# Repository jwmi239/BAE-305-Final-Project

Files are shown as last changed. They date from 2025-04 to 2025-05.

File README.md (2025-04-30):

# BAE-305-Final-Project
This repository contains all of the files associated with the BAE 305 final project.
## Project Summary

This report outlines the design, creation, and testing of a remote-control (RC) car intended for both the use of children and RC enthusiasts. In the original design concept, the user was intended to use radio connections to wirelessly control a four-wheel-drive, four-wheel-steer RC car programmed and powered by an Arduino Uno microcontroller. Additional features originally included a speedometer, a visual display, and car noises corresponding with the acceleration of the car. In the final product, the car was two-wheel-drive and two-wheel-steer and included features such as a handheld Bluetooth controller (as opposed to radio), an ultrasonic sensor serving as a safety feature, and a horn that plays the UK fight song. Through various testing phases, such as testing motor control via Bluetooth and iterating steering control to improve alignment, the RC car was completed and fully functional. 

## Design Description

### Bluetooth Wireless Connection

#### Materials

- HC-05 Bluetooth Module  
- Breadboard  
- Jumper wires  
- Raspberry Pi 3  
- Arduino Uno  
- 8BitDo Zero 2 Controller  

#### Assembly Procedures

First, the communication between the Raspberry Pi 3 and Arduino Uno was created. Once the HC-05 Bluetooth module was acquired, it was plugged into a breadboard and wired to the Arduino via jumper wires. It was connected to the 5V power rail and ground, the RX pin was connected to the software TX port, and the TX pin was connected to the software RX port. On the Raspberry Pi, no additional hardware was needed, as it has native Bluetooth capabilities. Serial communication and Bluetooth pairing were enabled by modifying the /boot/config.txt and disabling the serial console via raspi-config and using the bluetoothctl menu. The HC-05 was put in pairing mode by pressing and holding its button while powering it, which caused the onboard LED to blink rapidly. The Raspberry Pi then scanned for devices, paired with the HC-05, and trusted the connection. Once paired, the HC-05 was assigned a virtual serial port (e.g., /dev/rfcomm0), which is called in the main Python script. 

Once this connection was made, the 8BitDo Zero 2 gamepad was integrated via a wired USB connection to the Raspberry Pi. The controller was initialized in D-Input mode by holding the Start + Y buttons before connection, allowing it to register as a standard USB gamepad. Once connected, the Raspberry Pi automatically recognized the controller as /dev/input/js0. Functionality was verified using the jstest utility. Python was used to display button inputs to map button and directional inputs to specific vehicle actions, such as motor direction and auxiliary functions (playing the UK fight song).  



Figure 1: HC-05 Wiring Diagram

### Ultrasonic Sensor 

#### Materials
-	HC-sr04 ultrasonic distance sensor
-	4 male-female jumper cables
#### Assembly Procedures
Connect all four jumper cables to the HC-sr04, ensuring to note which wires connect to certain pins (Ideally using color coding to distinguish functions, such as red for power and black for ground). Connect the VCC pin of the Ultrasonic distance sensor to the 5V source of the Arduino. Connect the GND pin of the Ultrasonic distance sensor to any of the ground pins on the Arduino. Connect the Trig pin on the ultrasonic distance sensor to pin 6 on the Arduino, and the Echo pin to pin 7 on the Arduino. Ensure that each of the pins are connected to the correct pin on the Arduino before powering on.
### Steering

#### Materials
  -	¼” – 20 tpi Hardware
  -	3D printed Steering Components
    -	Steering Knuckles
    -	Drag Links
    -	Front Carriage
  -	SG90 Servo and Included Lever (Pitman arm)
  -	1/8” Cotter Pins

#### Assembly Procedures
The steering system is simple to assemble, creating an intuitive assembly and maintenance process. 

Step 1: Bolt the front carriage under the base of the car using three ¼” bolts



Figure 2: Steering System Assembly Step 1

Step 2: Install steering knuckle on each side of the front carriage using two ¼” bolts



Figure 3: Steering System Assembly Step 2

Step 3: Bolt Servo mount to base of car using two ¼” bolts and install the servo



Figure 4: Steering System Assembly Step 3

Step 4: Connect the servo to each steering knuckle with respected drag links, cotter pin each connection



Figure 5: Steering System Assembly Step 4

Step 5: Bolt wheels to the outside face of each steering knuckle using a ¼” bolt



Figure 6: Steering System Assembly Step 5

Step 6: The servo is then wired using 5V for power, one power signal from a PWM pin, and a ground. The Arduino is coded to send an output for left and right turns at 45° based on the input from the controller. 



Figure 7: Steering Servo Wiring Schematic

### Body

#### Materials
-	3D printed components
    -	Cab 
    -	Front Clip
    -	Bed 
    -	Bed Cover
-	SparkFun inventor’s kit
    -	Motor driver
    -	Motor x2
-	9V battery

#### Assembly Procedures
The body was designed to be easily assembled and removed. There is a ridge formed along the bottom of each body panel which simply slides over the aluminum base plate. When each body panel has been attached to the base, route the wires between the bottom of the bed and the base plate and connect them according to the schematic below. Finally, turn the battery packs on and place the bed cover in position to shield the electrical components.



Figure 8: Wiring for Motors and Motor Driver

### Speakers

#### Materials

- Arduino 
- DFPlayer Mini 
- 1W 8 Ohm speaker 
- 680 Ohm resistor 
- 1K Ohm resistor 
- 9V battery 
- 8705 Voltage Regulator 

#### Assembly Procedures

The Speaker assembly consisted of multiple interconnected pieces. The wiring can be found in Figure 9. First, the Arduino was connected to the RX and TX pins of the DFPlayer mini. The RX of the player was connected through a parallel circuit that had two paths starting from the Arduino digital pin. The first path ran through a 680 resistor then split to the player. The second path after running through the 680 resistor, ran through a 1K resistor and to ground. This allowed the Arduino to control when the player functioned. The player controlled the sound, sourcing it to a 1W speaker to amplify the sound. The speaker connected to the SPK1 and SPK2 pins in the player. To power the speaker, a 9V battery was wired as the power source. The battery ran through a voltage regulator to set 5V and 1.5A to the DFPlayer. The voltage regulator output pin connected to the Vin of the player, supplying the necessary power to run the speaker. 

The Arduino IDE code used a downloadable DFPlayer library. After a few set up functions, the DFPlayer Mini could play a specific file from the command “MP3player.play(#)” where # corresponds to the desired sound file number. Sound functions within the system at three separate points. The player functions from the second Arduino. First, an engine sound plays resulting from changes in acceleration. The DFPlayer command was integrated into an if statement for when the accelerometer reads a value above a threshold. The other two sounds, the UK fight song and the reverse sound, function in the same way—however the logic set to run them are found on the first Arduino. The Arduino 1 code sends a signal to Arduino 2 when a specific button is pressed for the fight song and the car is reversing for the reversing sound. Each sound plays through the audio file. The full code can be found in Results. 

ChatGPT Image Apr 24, 2025, 07_51_10 PM

Figure 9: Circuit Diagram for the sound components of the RC car. This wiring diagram was generated by ChatGPT 4o Ai

### Lights

#### Materials

- LED x2 
- 1K Ohm resistor x2 

#### Assembly Procedures

Two LEDs were added to the car in the same way. The circuit for these LED’s are simple and direct, with few components. Fed power from the Arduino, the circuit path flows from a digital pin to the 1K resistor in the breadboard, to the LED, to ground. The LED’s did not share a digital pin, as to allow them to be controlled separately. For the circuit diagram, see Figure 10.

LED circuit diagram image

Figure 10: Circuit Diagram for the LED circuit. This is repeated for the second LED circuit

## Design Discussion

### Bluetooth

Bluetooth was chosen as the means for communication rather than traditional radio. While traditional radio does not require pairing or draw the amount of power that Bluetooth does, Bluetooth was chosen for its ease of integration with both of the microcontrollers being used in the project. The Pi is natively compatible with Bluetooth devices, and the Arduino merely needed an inexpensive Bluetooth module (HC-05). Apart from the occasional disconnection due to the power demands of the module, this made connection seamless after the initial connection to the Pi was made.  

Future designs may employ Bluetooth for additional features to the car. Supplemental power sources may be needed to prevent the disconnection of the module from the Pi. 

### Distance Sensing

### Steering
To create a more realistically functioning car, we decided to model the steering after a two-wheel bell crank. The bell crank method uses a two-link system connected to each wheel that allows both wheels to turn from a single servo, similar to actual automobiles. This is done through a series of steering components, which includes a pitman arm, steering knuckles, and drag links. The goal with this system was to create what is known as Ackermann geometry. A steering system is considered to be Ackermann steering if the inside wheel is at a sharper angle than the outside wheel while turning. This is the case with the bell crank system, as seen below.



Figure 11: Ackermann Steering Angle Phenomenon

With the pitman arm at a center-point, equal length drag links, and mirrored geometry for the steering knuckles, this creates a sharper angle for the side that the servo is turning away from. If not for this phenomenon, the inside wheel would be fighting the ground during turns due to travelling on a smaller turning radii than the outside wheel, as shown below. Ackermann steering allows for less wear on tires, steering components, and axle gearing if applicable. 



Figure 12: Inside wheel vs. Outside wheel Turning Radius 
### Sound

The car contains a sound component that functions as a final output for multiple logic systems. The sound for the car functions through a DFPlayer Mini. The DFPlayer is an MP3 module for the Arduino. The DFPlayer Mini was chosen as the sound playing device because of its easy integration with the Arduino system. Arduino IDE has a downloadable library for the DFplayer that allows audio to be integrated into the code with a few simple commands. For this application, the DFPlayer Mini connects to a 1W speaker that projects the sound. Housing a micro-SD card, the player runs MP3 audio files when directed by the Arduino microcontroller.  A voltage regulator and 9V battery were used to ensure the system received adequate power. The 9V supplied the voltage, and the regulator ensured adequate current flowed through the DFPlayer and to the speaker.  

### Lights

Lights were an added design feature of the car. These lights were to signal as the car turned. LED’s were chosen because they are often used in Arduino projects, and the bright colors add an additional sensory element for users. Individual LED’s were chosen over a strip of lights due to the high demand for current needed to sustain brightness in a longer string of LED’s. The entire car already had 9V batteries and 5V power packs, so it was determined unnecessary to add additional power sources for just the lights. Additionally, the singular LED’s mimicked the turn signals of a car, fitting well with the theme for the project. 

## Testing Procedures

The testing of the car took place in several phases as each feature was completed, as well as a final “sprint” to integrate all features.  

The first feature to be completed was the establishment of the wireless connection. A series of tests were completed for each leg of communication previously mentioned. First, the communication between the Raspberry Pi 3 and Arduino Uno was tested. Once the HC-05 Bluetooth module was running on the Arduino, serial communications were opened on both the Arduino and Pi. The HC-05, acting as the slave, was sent serial messages via the assigned serial port from the Pi to confirm its connection. Once the connection between the Pi and Arduino was secured, attention was turned to connecting the 8BitDo controller to the Pi. The controller was wired to the Pi via USB—similar to how a keyboard would work with the Pi. To determine what messages each button of the controller was sending upon being pressed, a short python script was created and used to read the button press events. These outputs were recorded and used in the development of the primary code. 

Another feature that needed to be completed and tested was sound. Initially, based on the DFPlayer specifications a 3W speaker was chosen. This speaker was the top of the power output range for the player. When in a system that ran solely the DFPlayer and the speaker, the sound worked without issues. When integrating with the system however, the speaker size proved to be an issue. Given the power demand of the 3W speaker, the addition of the sound system was creating a power need that exceeded the output capabilities of the Arduino. Consequently, the sound quality decreased, and other components of the car would not run when the speaker was playing. The necessary solution was switching to a different speaker that could use a smaller amount of power. Therefore, a 1W speaker was selected to replace the 3W speaker. This speaker was wired in the same way as the original speaker. This set up worked the first day it was implemented, however the following day had additional issues: giving loud low pitch feedback and not playing the desired mp3 files. A 9V battery was added to be the power source for the player and speaker. Wired through the Arduino however, this did not fix the issue as the Arduino limited the current flow of the circuit. To resolve this issue, a voltage regulator was incorporated. The voltage regulator connected to the 9V rather than the Arduino, supplying a 5V and 1.5 A to the DFPlayer and speaker. This resolved the sound issues. 

Lights were another feature that needed to be tested and integrated. Initially, it was planned to use an LED strip to maximize the appeal of the LED. In the inital testing of the LEDs it was determined that 5V from the Arduino was not sufficient to run the strip. This LED strip would require an additional power source to supply enough current to maintain light for many LEDs. Once additional power sources were acquired for the motors, the LEDs were revisited to see if they could be powered. During this testing, a 9V battery was wired through the 5V pin of the Arduino rather than the necessary Vin pin. This issue caused the computer connected to the Arduino to receive 9V of back voltage and stop working. Individual LEDs were chosen to be used over the strip due to the lack of need for additional power. These LEDs wired directly to the Arduino and were controlled from HIGH and LOW commands through a digital pin. 

The steering system also proposed a few challenges. The code was simple, just a few lines taken from online sources and tailored to the needs of this project. The CAD modeling resulted in relatively smooth implementation of the moving parts. However, the first iteration of the steering knuckles did not have clearance for the “lug nuts” and required more drop to allow for them. Connection methods for the drag links were also a point of testing. The holes were too small to reasonably use bolts and screws would’ve inhibited the rotation during turning. 

## Results



Figure 13: Complete car assembly

## Discussion

Throughout the project, there were multiple challenges and complications that needed to be overcome to complete the deliverables. These challenges molded the final project into what is presented in this report. The WildCar completed each deliverable it set out to do: two-wheel drive, two-wheel steering, wireless Bluetooth control, Lights synced to turning, revving sound from acceleration, beeping upon reversing, playing a song from a controlled input, and stop when too close to an object-- all integrated into a covered complete car design. 

Bluetooth control of the car proved to be both one of the most prominent features and drawbacks of the car. Proving difficult to set up and maintain manually, Bluetooth through a Raspberry Pi was an effective means of remote communication when connected. The system communicated with little delay and the signal transmitted without error. Bluetooth as incorporated in this system, however, had many drawbacks that would limit how well the project could be extrapolated to other projects. First, the connection needed to be manually established. The connection would often get lost, and the connection process repeated. Additionally, using the Pi as a relay from the controller and communicator to the Arduino proved to be an added layer of complexity. Navigating the Pi system was not user friendly and minimally added to the effectiveness of the project. While it did increase the range of connection when compared to the controller and Arduino alone, it was still limited by the inherent limitations of Bluetooth (about 30ft). Higher quality controllers or radio controllers are available for purchase that have greater range, and can cut out the Pi as an intermediate, effectively communicating directly with the Arduino. 

Another limitation with the WildCar design is in regard to power. The Ardunos are only capable of 5V power output with a power pack. Many parts of the design required greater power to run sufficiently when integrated. The final design required two 5V power packs and two 9V batteries. The design was limited by these sources because the batteries would quickly drain and require replacement. The power sources, whilst rechargeable, faced similar issues. The system did supply power effectively, and each component functioned properly with the power supplied. Multiple sources also allowed for each component to receive the specific power needed independently. Performance would decrease as the power drained. A higher quality single power supply would allow for a more integrated design, would last longer, and clean up the wiring. As seen in the use of a voltage regulator to meet the specific needs of the speaker, power output could be modified as needed to meet individual needs of components. A better power supply would also allow the car to run longer at full performance.  

The code for the steering system worked as expected with the lines given online. Integration was easy, as the controller was already connected via Bluetooth to send input to the servo. Another easy fix came through the implementation of cotter pins for the linkage connections; the pins are small enough and allow for rotation during turning. The last step was to add clearance for the lug nuts, which was done through a second iteration of 3D printed steering knuckles. This allowed for tightening of the entire steering system, and brought the car closer to having true Ackermann steering geometry.

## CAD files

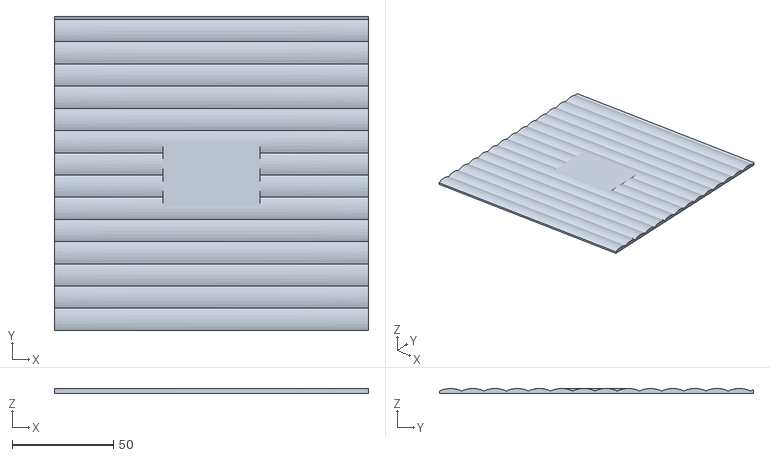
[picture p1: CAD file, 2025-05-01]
Truck cover.stl
155.0 x 155.0 x 2.50

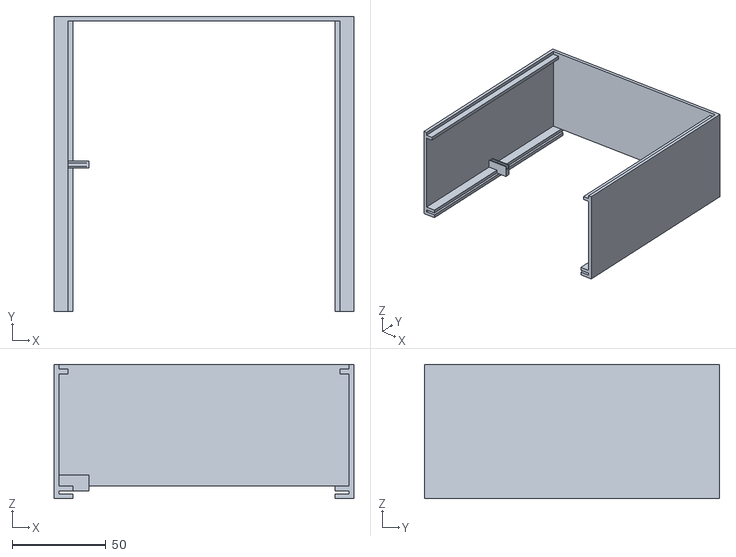
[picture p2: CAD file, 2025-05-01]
TruckBed.stl
160.0 x 157.5 x 71.5

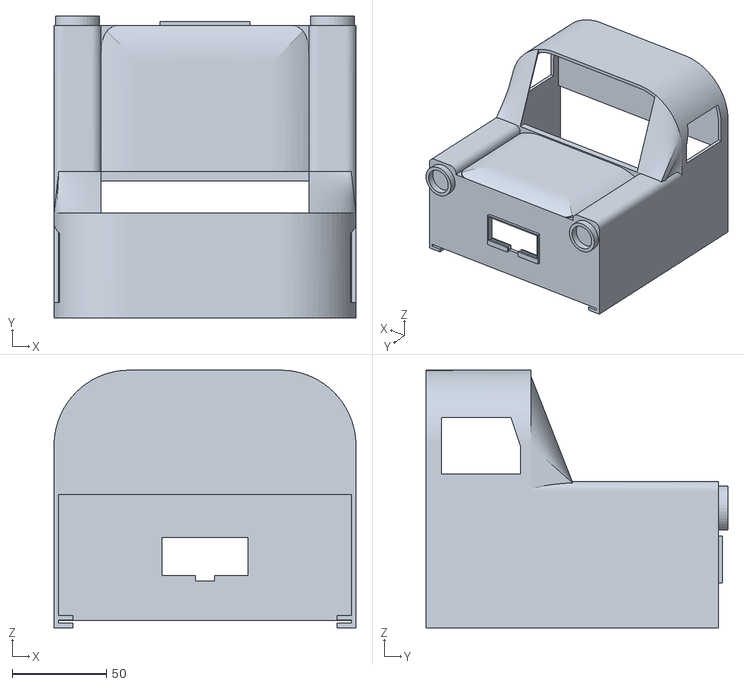
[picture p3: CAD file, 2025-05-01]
CarFront.stl
160.0 x 160.0 x 136.6

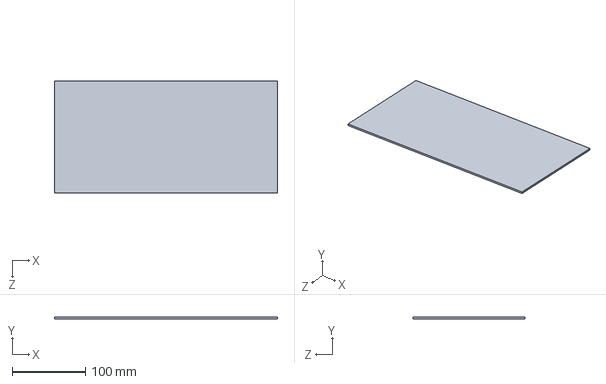
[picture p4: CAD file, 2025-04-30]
BAE 305 Car Frame.SLDPRT
304.8 x 2.54 x 152.4 mm

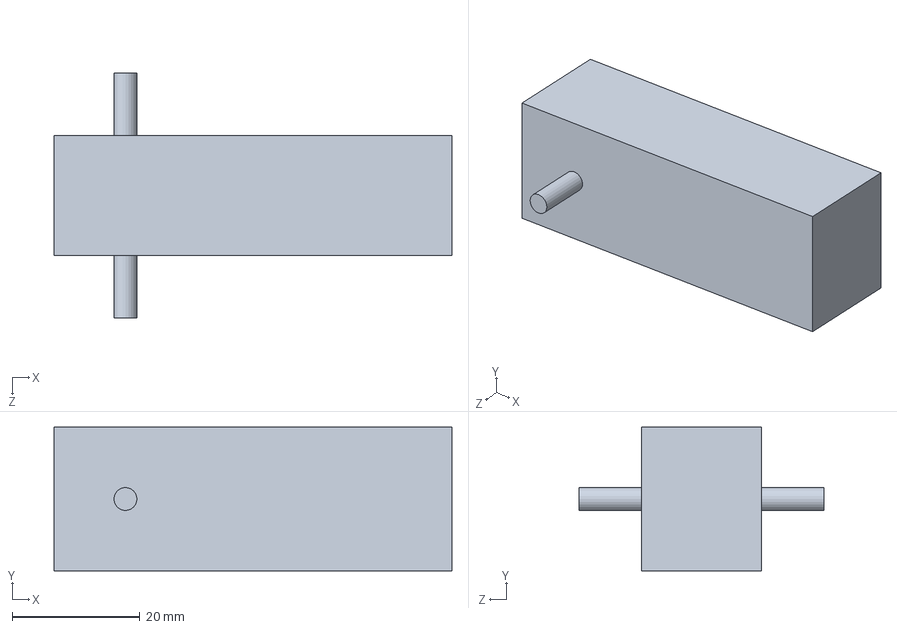
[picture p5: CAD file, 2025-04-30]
BAE 305 Motor.SLDPRT
62.4 x 22.5 x 38.4 mm

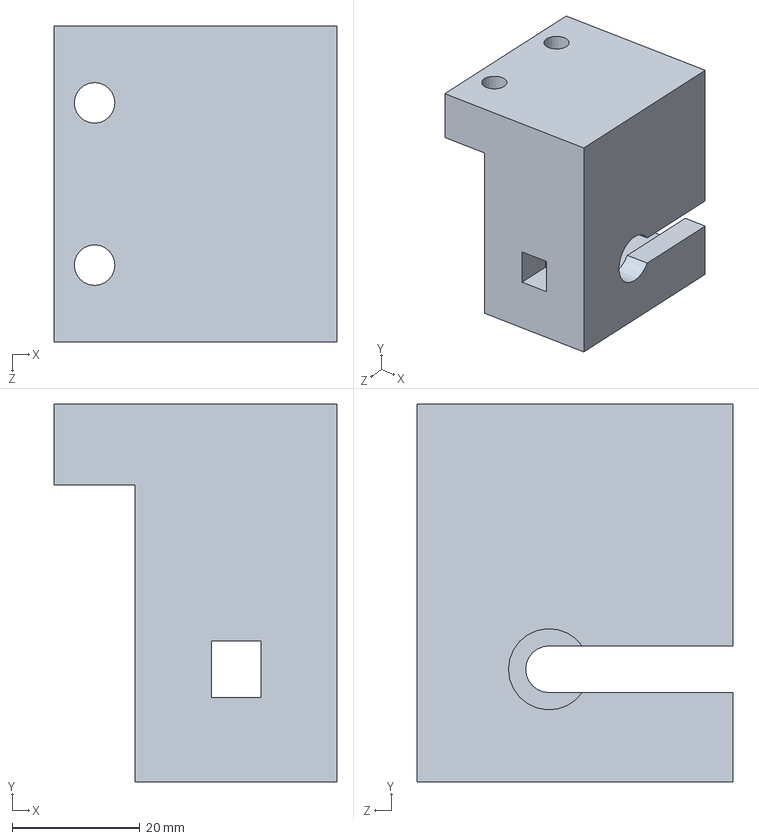
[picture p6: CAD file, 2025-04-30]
BAE 305 Car Passenger Motor mount.SLDPRT
44.3 x 59.2 x 49.5 mm

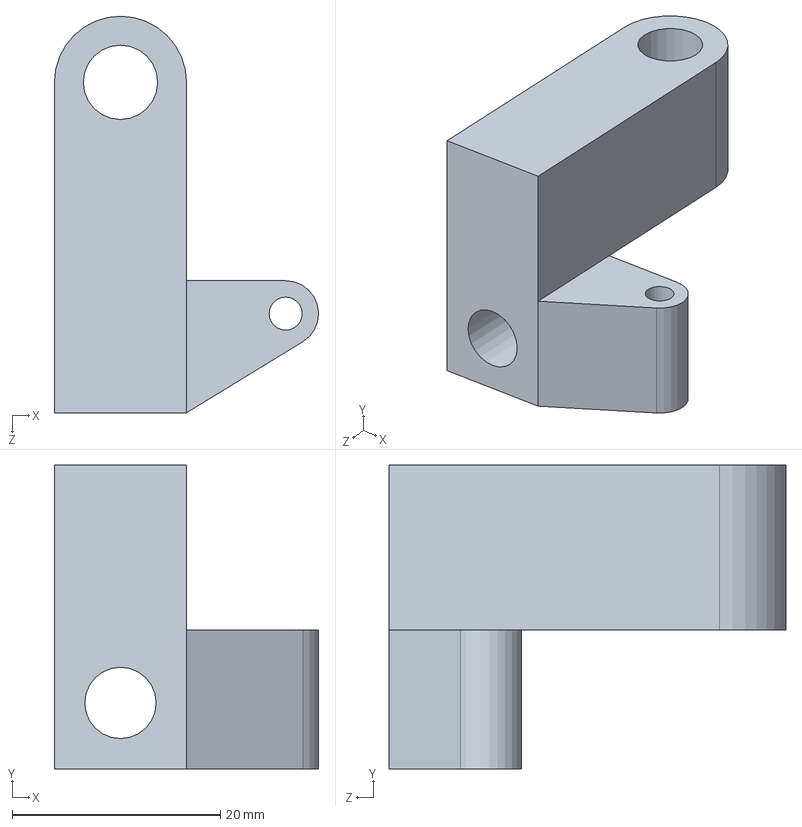
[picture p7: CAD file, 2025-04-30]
BAE 305 Steering Knuckle.SLDPRT
25.4 x 29.2 x 38.1 mm

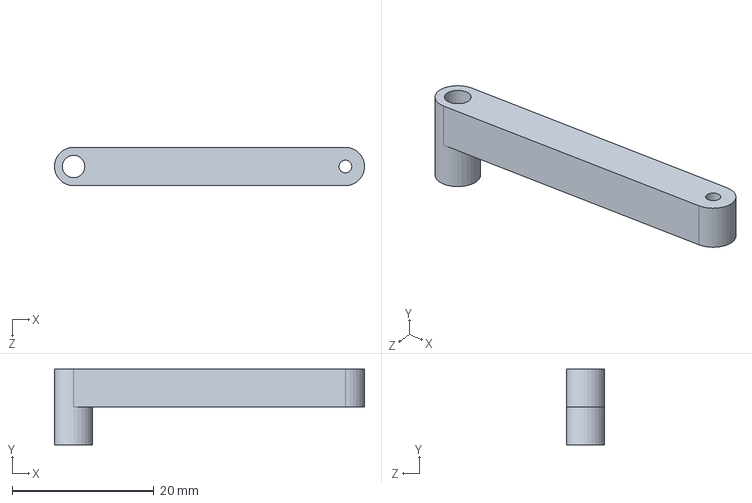
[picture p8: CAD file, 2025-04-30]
BAE 305 Tie Rod Passenger.SLDPRT
43.7 x 10.7 x 5.40 mm

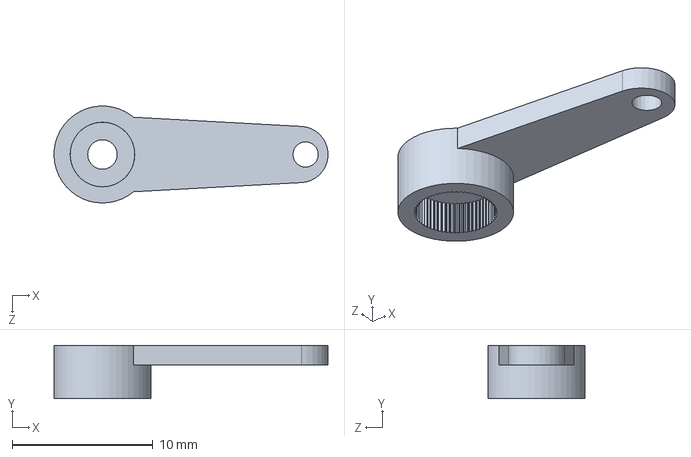
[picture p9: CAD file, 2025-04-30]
SG90 Arm.SLDPRT
19.5 x 3.80 x 6.90 mm

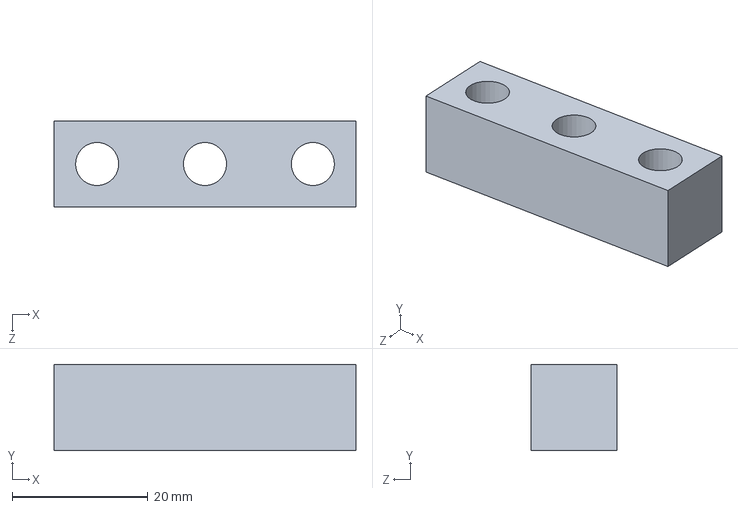
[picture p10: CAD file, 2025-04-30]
BAE 305 Front end bottom.SLDPRT
44.5 x 12.7 x 12.7 mm

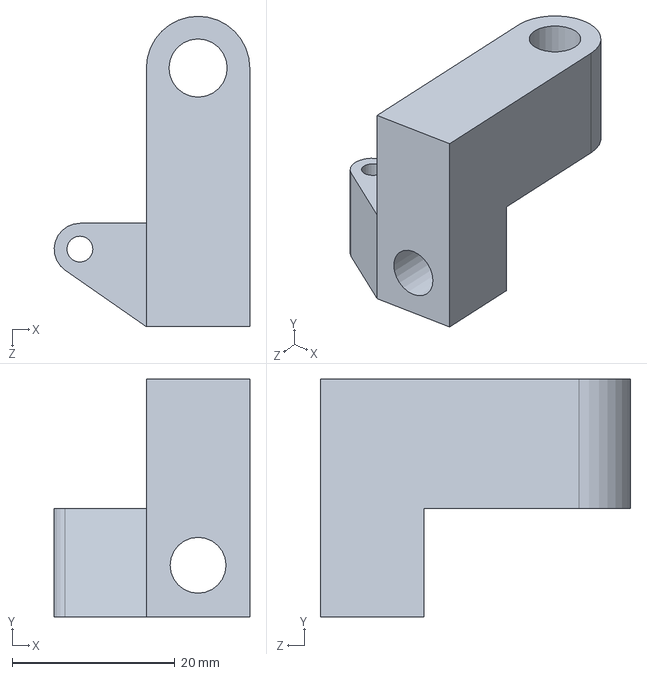
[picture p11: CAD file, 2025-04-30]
BAE 305 Opposite Steering Knuckle.SLDPRT
24.0 x 29.2 x 38.1 mm

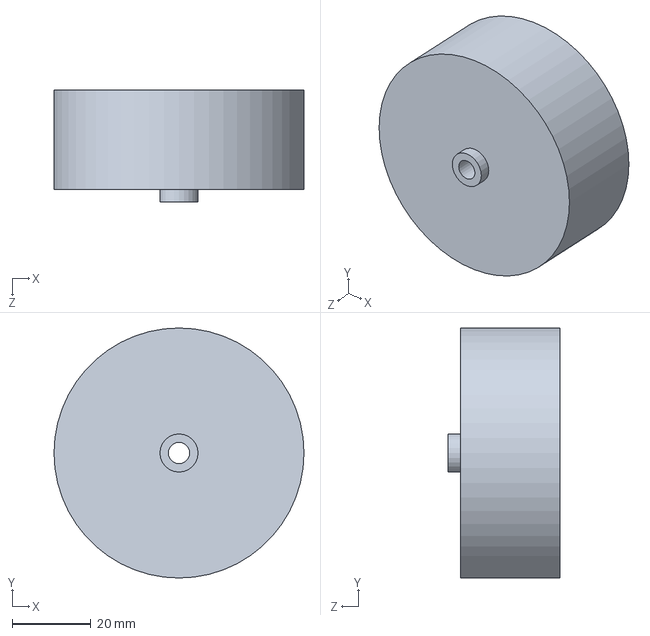
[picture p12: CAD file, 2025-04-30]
BAE 305 Wheels.SLDPRT
63.5 x 63.5 x 28.6 mm

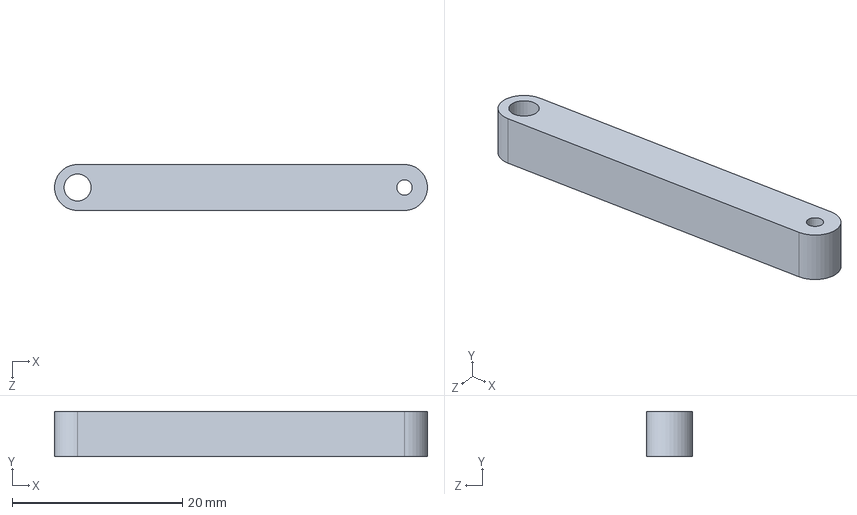
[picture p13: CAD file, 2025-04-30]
BAE 305 Tie Rods.SLDPRT
43.8 x 5.33 x 5.40 mm

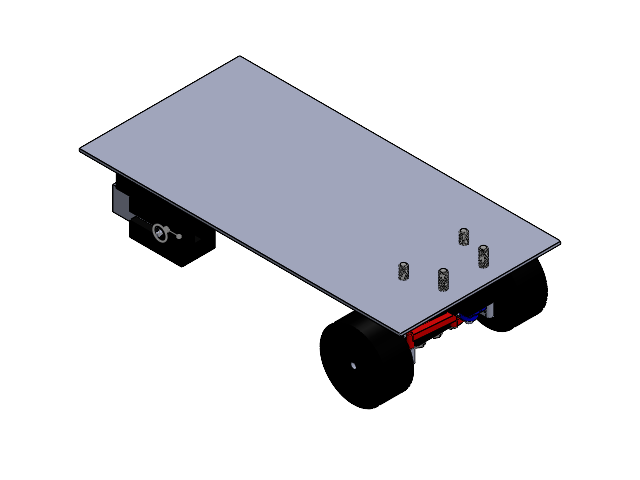
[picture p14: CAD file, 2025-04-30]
BAE 305 RC CAR.SLDASM
BAE 305 Car Frame
BAE 305 Motor
BAE 305 Wheels x 2
BAE 305 Steering Knuckle
BAE 305 Opposite Steering Knuckle
BAE 305 Car Front end
SG90 - MotorOutput
SG90 Arm
BAE 305 Tie Rods
BAE 305 Tie Rod Passenger
BAE 305 Servo mount
BAE 305 Front end bottom
92620A542_Zinc Yellow-Chromate Plated Hex Head Screw x 7
BAE 305 Car Passenger Motor mount
BAE 305 Car Driver Motor mount

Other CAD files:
BAE 305 Car Driver Motor mount.SLDPRT
BAE 305 Servo mount.SLDPRT
BAE 305 Car Front end.SLDPRT
SG90 - BasePart.sldprt
SG90 - MotorOutput.sldprt

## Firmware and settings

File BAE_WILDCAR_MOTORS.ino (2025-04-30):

#include <SoftwareSerial.h>                 //Imporing of necesarry Libraries
#include <Servo.h>

SoftwareSerial BTSerial(3,2);               // Bluetooth (RX,TX) as arduino sees it

const int trig = 4;                         // Pins for Ultrasonic distance sensor
const int echo = 5;                         //

const int LeftLED = 7;                      //Pins for turning signal LEDs
const int RightLED = 6;

const int AIN1 = 8;                         //Pins for motor Driver
const int AIN2 = 9;
const int PWMA = 10;
const int Servopin = 11;                    //Pin to control Servo motor

const int arduinoConnection1 = 12;          //Pins to connect to second arduino
const int arduinoConnection2 = 13;

Servo myServo;                              //Instantiates a servo object

int motorSpeed = 250;                       //initialization of global variables to be used by program
int centerPos = 90;
int leftPos = centerPos - 45;  
int rightPos = centerPos + 45; 
float duration, distance;
char command;

void setup() {
  pinMode(AIN1, OUTPUT);                    //Set pins associated with motor driver to be outputs
  pinMode(AIN2, OUTPUT);
  pinMode(PWMA, OUTPUT);
  pinMode(trig, OUTPUT);                    //Set pins for the Ultrasonic sensor to be input/output respectively for trigger and echo
  pinMode(echo, INPUT);
  pinMode(LeftLED,OUTPUT);                  //Set pins associated with LED indicators to be outputs
  pinMode(RightLED,OUTPUT);
  pinMode(arduinoConnection1,OUTPUT);       //set connection Pins to be output pins
  pinMode(arduinoConnection2,OUTPUT);

  BTSerial.begin(9600);                     //Begin serial communication with the HC-05
  myServo.attach(Servopin);                 //Tell the servo which pin it is attached to so that its internal methods function correctly 
  myServo.write(centerPos);                 //Write the location of the servo motor to be the center position that we want
  }

void loop() {
  
  digitalWrite(trig, LOW);                  //Trigger the Ultrasonic distance sensor to emit a recoverable signal
  delayMicroseconds(2);
  digitalWrite(trig, HIGH);
  delayMicroseconds(10);
  digitalWrite(trig, LOW);

  duration = pulseIn(echo, HIGH);           //Collect information about the ultrasonic signal and calculate the distance from the car to an obstacle
  distance = (duration*0.0343)/2;
  delay(100);
  
  if (distance <= 10 ){                    //Check if the car is too close to something
    if (BTSerial.available()) {            //Allow the car to check the bluetooth because the user will want to reverse still if they got too close to something

      command = (char)BTSerial.read();

      if (command = 'B'){
         // B = full backward
        spinMotor(-255);
        digitalWrite(arduinoConnection1, LOW);      //Inhibit playing of UK fight song sound
        digitalWrite(arduinoConnection2, HIGH);     //Play reversing sound
      }else{
        spinMotor(0);
        digitalWrite(arduinoConnection1, LOW);      //Inhibit playing of UK fight song sound
        digitalWrite(arduinoConnection2, LOW);      //Inhibit playing of Reversing sound
      }

    }else{
      spinMotor(0);
      digitalWrite(arduinoConnection1, LOW);        //Inhibit playing of UK fight song sound
      digitalWrite(arduinoConnection2, LOW);        //Inhibit playing of Reversing sound
    }
        
  }else{

    if (BTSerial.available()) {
      command = (char)BTSerial.read();                //Read in a character from the HC-05
          
      switch (command){                               //Interperet meaning of recieved character
        case 'F':
          // F = full forward
          spinMotor(255);
          digitalWrite(arduinoConnection1, LOW);      //Inhibit playing of UK fight song sound
          digitalWrite(arduinoConnection2, LOW);      //Inhibit playing of Reversing sound
          break;
        case 'B':
          // B = full backward
          spinMotor(-255);
          digitalWrite(arduinoConnection1, LOW);      //Inhibit playing of UK fight song sound
          digitalWrite(arduinoConnection2, HIGH);     //Play reversing sound
          delay(100);
          digitalWrite(arduinoConnection2, LOW);      //Inhibit constant restarting of reversing sound
          break;
        case 'S':
          // S = Complete Stop
          spinMotor(0);
          digitalWrite(arduinoConnection1, LOW);    //Inhibit playing of UK fight song sound
          digitalWrite(arduinoConnection2, LOW);    //Inhibit playing of reversing sound
          break;
        case 'L':
          //  L = Hard Left
          myServo.write(leftPos);                   //Put servo into left turning position
          digitalWrite(LeftLED, HIGH);              //Turn on Left turning signal
          digitalWrite(RightLED, LOW);              //Inhibit Right turning signal
          break;
        case 'R':
          // R = Hard Right
          myServo.write(rightPos);                  //put servo into right turning position
          digitalWrite(LeftLED, LOW);               //Inhibit Left turning signal
          digitalWrite(RightLED, HIGH);             //Turn on Right turning signal
          break;
        case 'C':
          //Return to center position         
          myServo.write(centerPos);                 //Return servo to center position
          digitalWrite(LeftLED, LOW);               //Inhibit Left turning signal
          digitalWrite(RightLED, LOW);              //Inhibit Right turning signal
          break;
        case 'W':
          //Play UK fight song on command
          digitalWrite(arduinoConnection1, HIGH);   //Play UK fight song  
          digitalWrite(arduinoConnection2, LOW);    //Inhibit playing of reversing sound
          delay(100);
          digitalWrite(arduinoConnection1, HIGH);   //Inhibit constant restarting of fight song
          break;
      }
    }
  }
} 

/********************************************************************************/
void spinMotor(int motorSpeed){ 

  if (motorSpeed > 0){                                //if the motor should drive forward (positive speed)  
    digitalWrite(AIN1, HIGH);                         //set pin 1 to high 
    digitalWrite(AIN2, LOW);                          //set pin 2 to low 
  }
  else if (motorSpeed < 0){ 
    digitalWrite(AIN1, LOW);                          //set pin 1 to low 
    digitalWrite(AIN2, HIGH);                         //set pin 2 to high 
  }else{                                              //if the motor should stop 
    digitalWrite(AIN1, LOW);                          //set pin 1 to low 
    digitalWrite(AIN2, LOW);                          //set pin 2 to low 
  }

  analogWrite(PWMA, abs(motorSpeed));                 //now that the motor direction is set, drive it at the entered speed 
}

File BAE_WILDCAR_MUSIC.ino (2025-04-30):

#include <SoftwareSerial.h>                                   //Import Necesarry Libraries
#include <Wire.h> 
#include <SparkFun_MMA8452Q.h> 
#include <DFRobotDFPlayerMini.h>

static const uint8_t PIN_MP3_TX = 5;                          //Set the Tx and Rx pins of the DFplayer
static const uint8_t PIN_MP3_RX = 4;

const int arduinoConnection1 = 12;                            //set up pins for communication from another arduino
const int arduinoConnection2 = 13;

SoftwareSerial softwareSerial(PIN_MP3_RX, PIN_MP3_TX);        //Begin a softwareSerial object for the DFPlayer so we can communicate with it
DFRobotDFPlayerMini MP3player;                                //Create a DFPlayer object so we can use its functions
MMA8452Q accel;                                               //create an accelerometer object to get acceleration readings

void setup(){

  Serial.begin(9600);                                         //begin serial communication with a computer (if available) and with DFPlayer
  softwareSerial.begin(9600);

  pinMode(arduinoConnection1, INPUT);                         //prepare arduino connection pins to revcieve signals
  pinMode(arduinoConnection2, INPUT);

  if (MP3player.begin(softwareSerial)){                       //Check is MP3Player is functioning correctly
    Serial.println("MP3 Player ready");
  }else{
    Serial.println("MP3 Player NOT READY");
  }

  Wire.begin();                                               //Begin a wire object that connects the accelerometer to the arduino using the SDA and SGL pins

  if (accel.begin() == false) {                               //Ensure the Accelerometer is connected
    Serial.println("Not Connected. Please check connections and read the hookup guide.");
    while (1);
  }

  MP3player.volume(30);                                      //set the volume of the speaker
  delay(500);
  MP3player.play(1);      //Should play Backing up noise *For troubleshooting*
  delay(5000);
  MP3player.play(2);      //Should play UK Fight song *For troubleshooting*
  delay(5000);
  MP3player.play(3);      //Should play Reving noise *For troubleshooting*
  delay(5000);
}

void loop(){
  Serial.print(digitalRead(arduinoConnection1)); //*For troubleshooting*
  Serial.print(digitalRead(arduinoConnection2)); //*For troubleshooting*

  if (accel.available()) {

    Serial.print(accel.getCalculatedX());//*For troubleshooting*
    Serial.print(accel.getCalculatedY());//*For troubleshooting*
    Serial.println(accel.getCalculatedZ());//*For troubleshooting*

    if(accel.getCalculatedZ()>=1.5){
      MP3player.play(1);
    }else if (digitalRead(arduinoConnection1) == "HIGH"){             //Checks if the DFPlayer should play the UK Fight song
      MP3player.play(2);
    }else if (digitalRead(arduinoConnection2) == "HIGH"){             //Checks if the DFPlayer should play the reversing sound
      MP3player.play(3);
    }
  }
}

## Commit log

2025-04-30 Added BT/wireless connection stuff, project summary, and testing procedures
2025-04-30 CAD files
    Everything except for the body
    [BAE 305 Car Driver Motor mount.SLDPRT, BAE 305 Car Frame.SLDPRT, BAE 305 Car Front end.SLDPRT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]
2025-04-30 Code Files
    Code for each arduino, and separate supporting code
